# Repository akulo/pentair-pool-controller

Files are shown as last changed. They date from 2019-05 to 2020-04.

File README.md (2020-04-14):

# Pentair Pool Controller

For last couple of years, I have been looking for good automation system that I can use to automate my backyard pool and spa. All current systems available are outdated and overpriced. It is mind blowing to see how much Pentair, Zodiak or Hayward are charging for their systems. So, I decided to build my own.

It is powered by RaspberyPi running NodeJS, Node-Red, Node Red Dashboard coupled with 16 relays module and IntelliComm® II Interface Adapter. I really could have implemented software solution instead of overpriced adapter but I decided to focus on building hardware first. 

### Here is the view of AQUALINK® POWER CENTERS and Pool Controller Altelix enclosure:
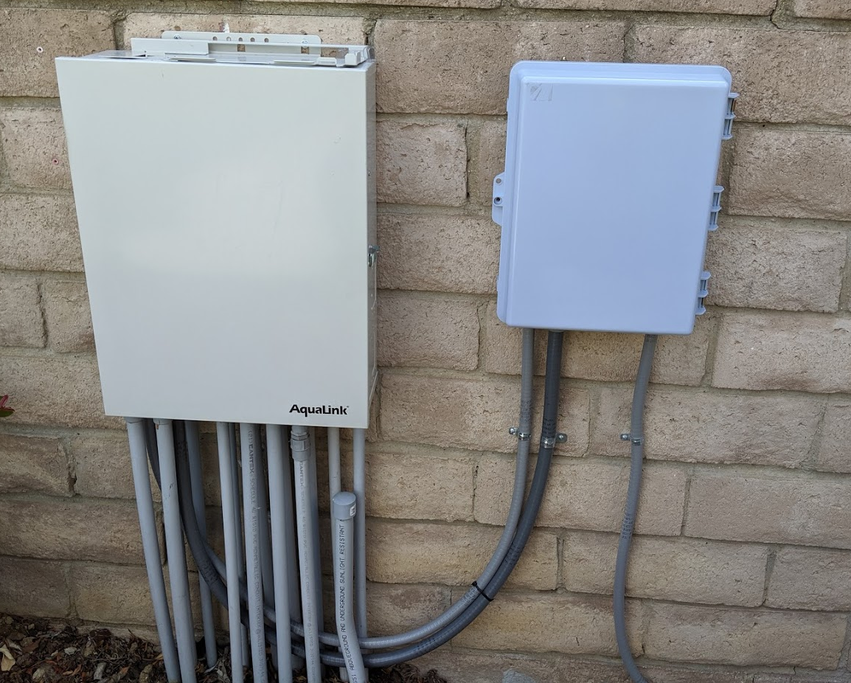
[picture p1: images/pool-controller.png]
Pentair Pool Controller


### View of assembled controller
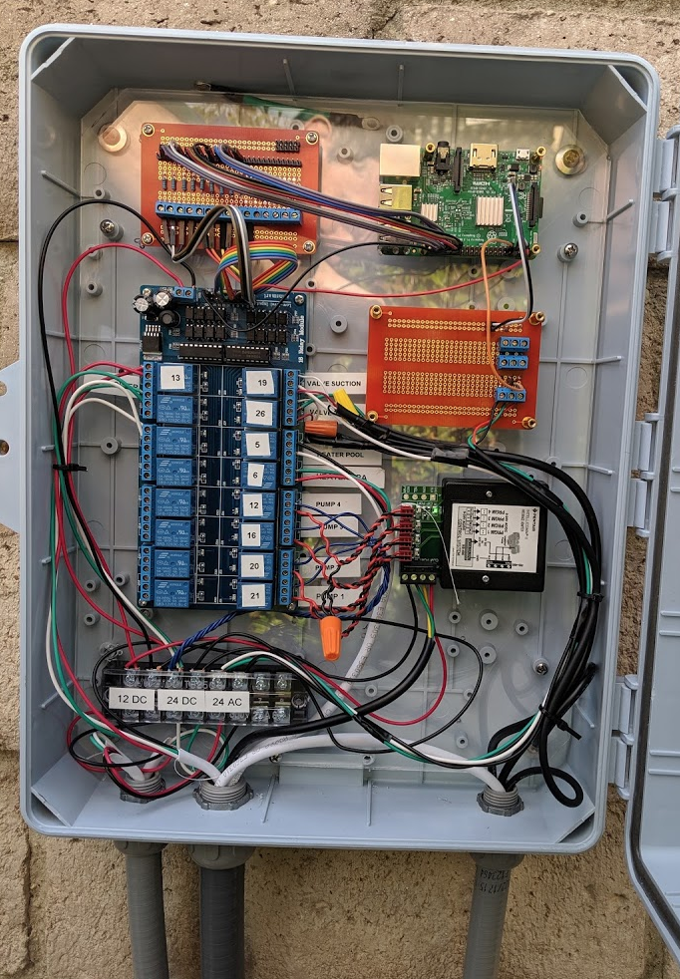
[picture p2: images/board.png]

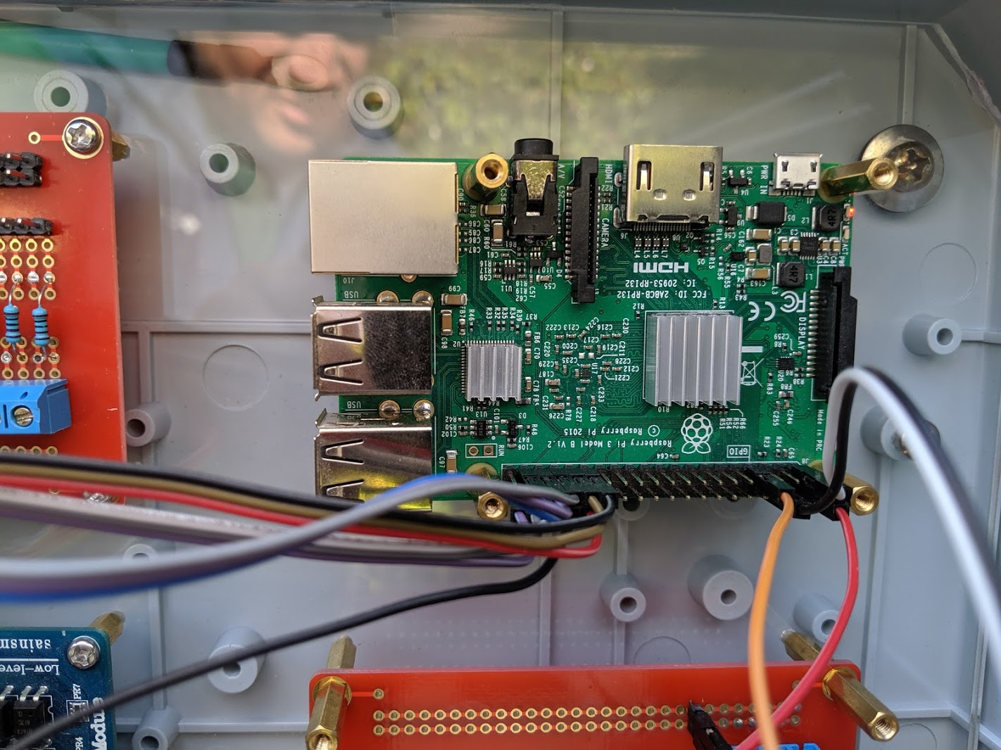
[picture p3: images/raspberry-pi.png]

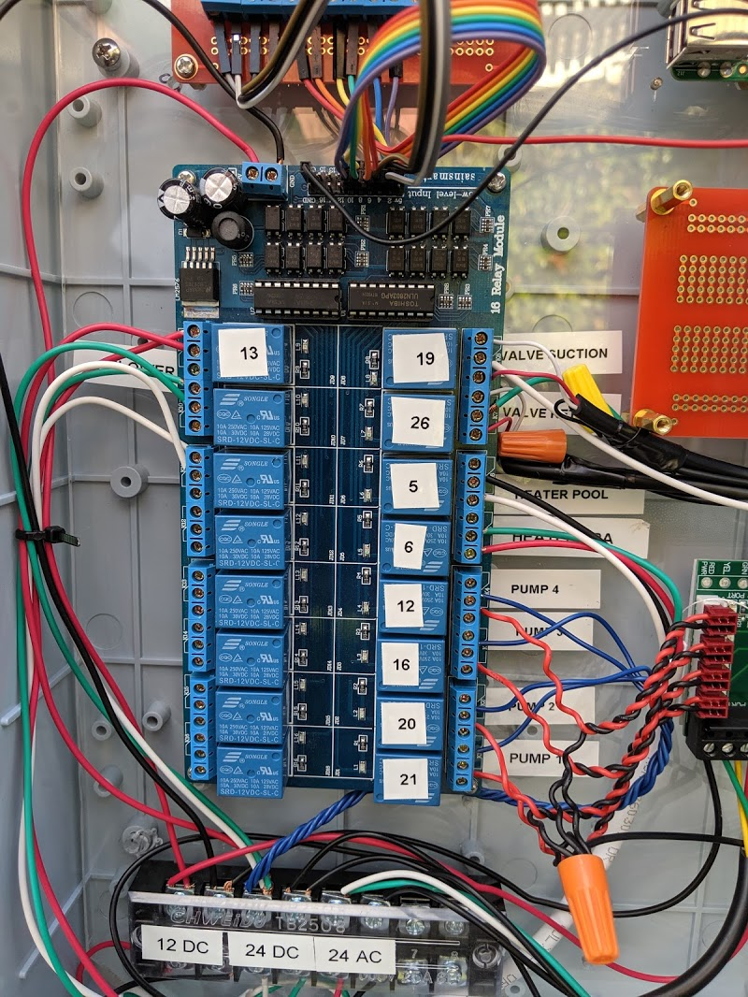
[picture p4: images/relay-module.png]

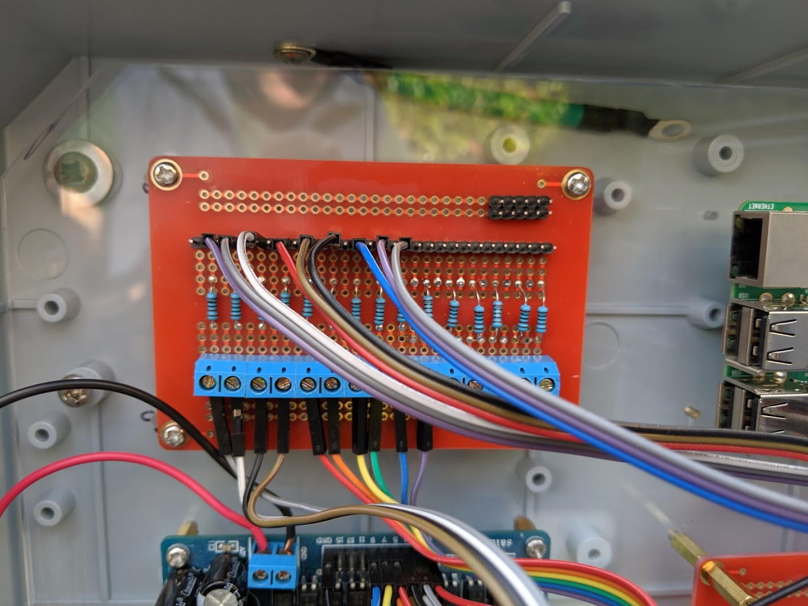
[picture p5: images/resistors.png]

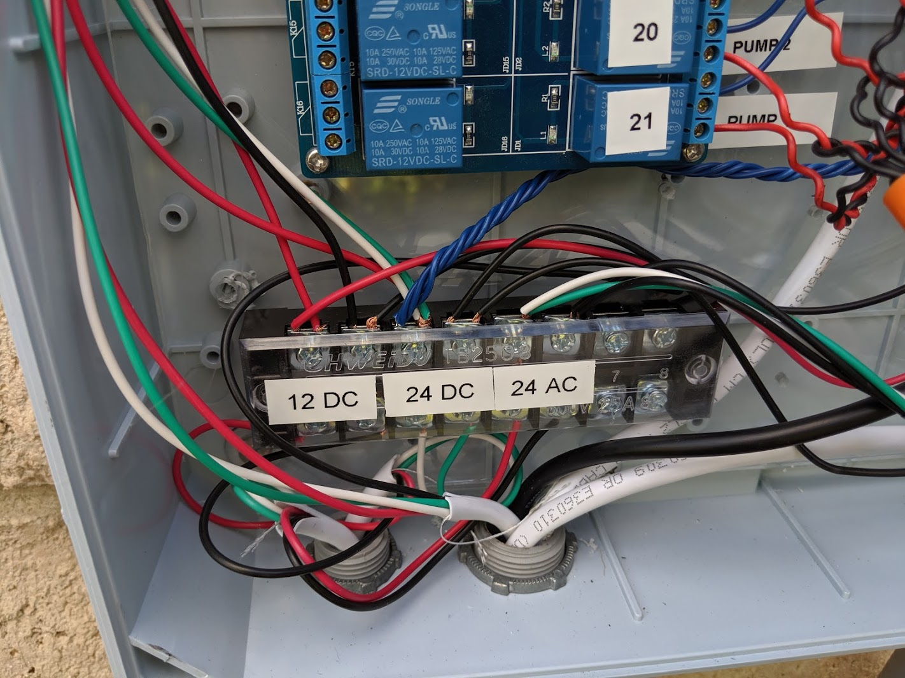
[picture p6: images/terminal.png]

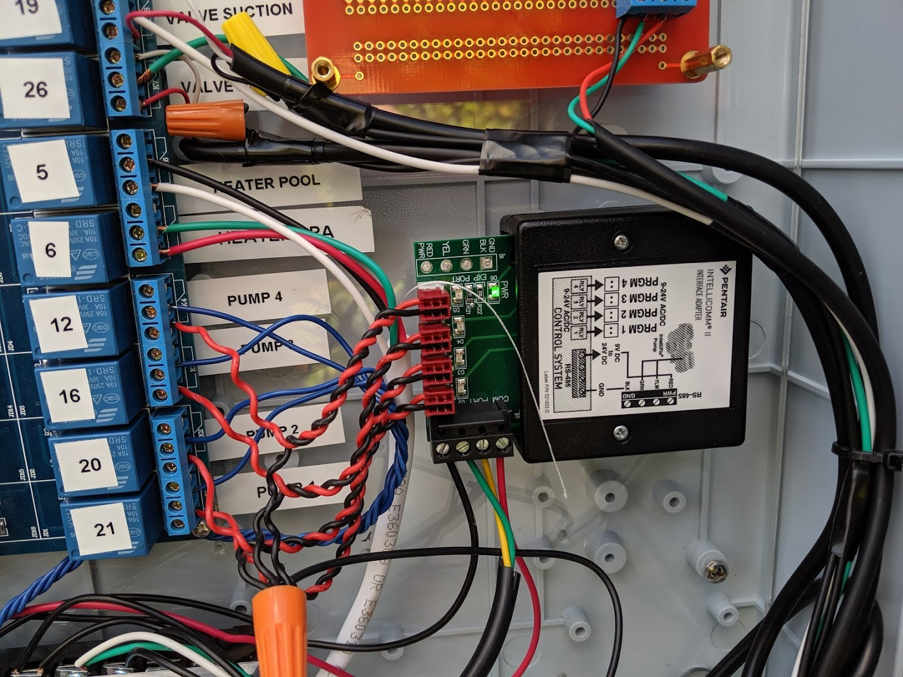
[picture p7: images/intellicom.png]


### View of Intermatic PE24VA Valve Actuators
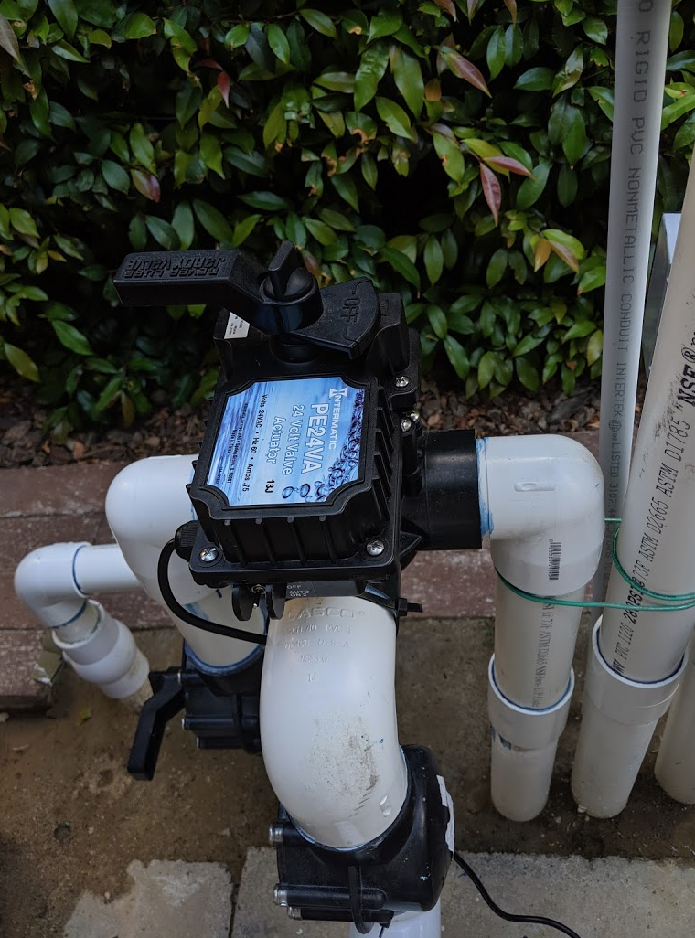
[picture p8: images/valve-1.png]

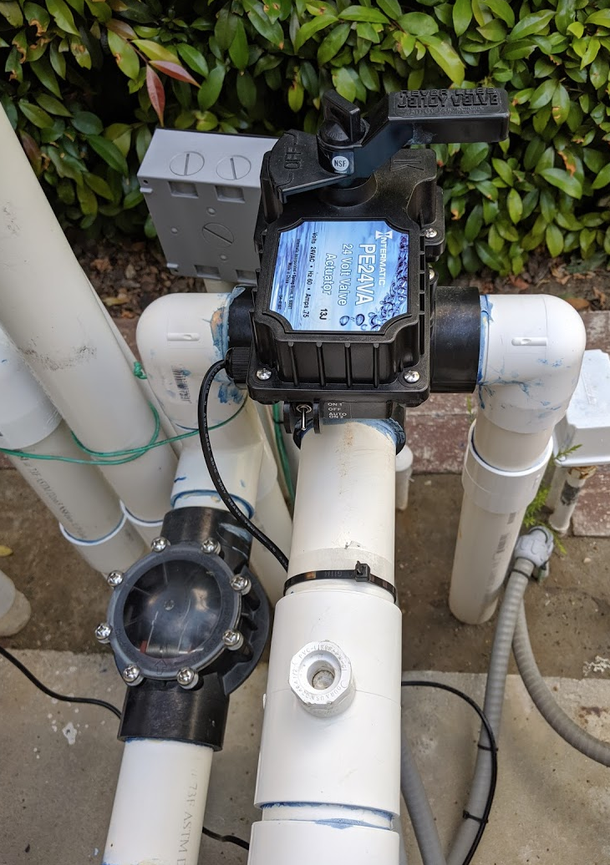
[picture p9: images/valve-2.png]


### View of sub-panel with breakers
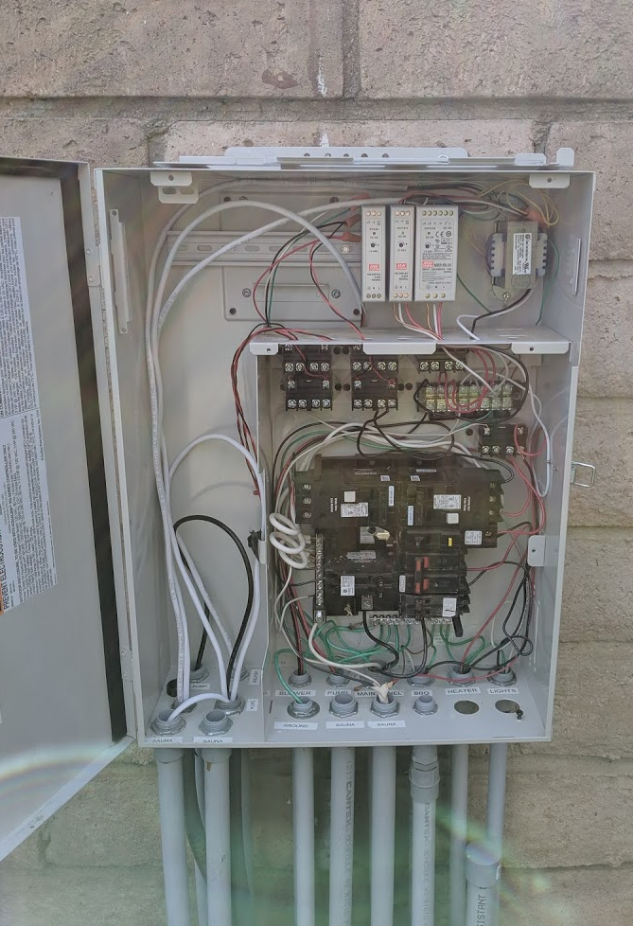
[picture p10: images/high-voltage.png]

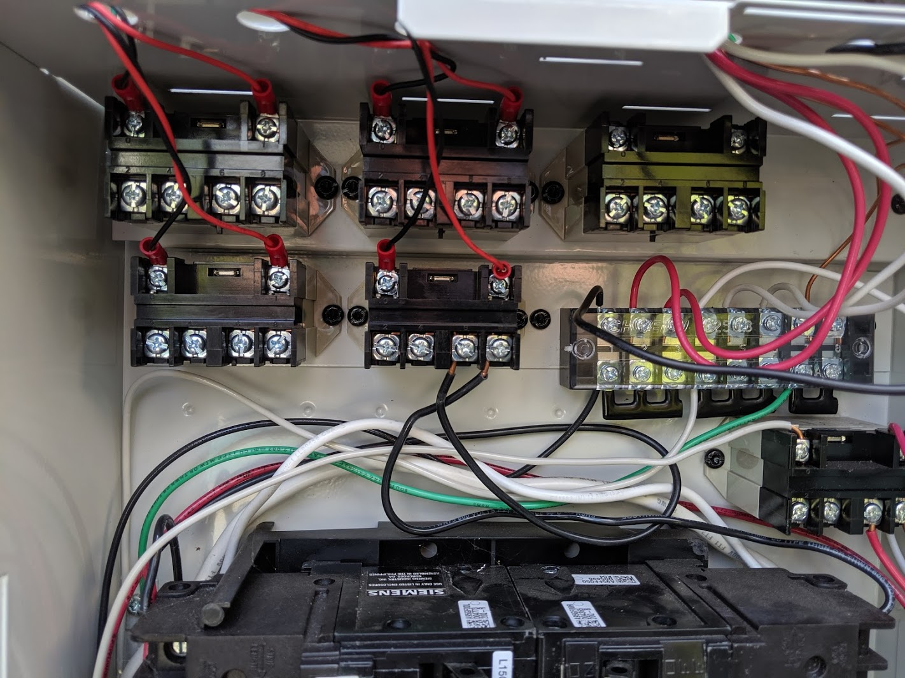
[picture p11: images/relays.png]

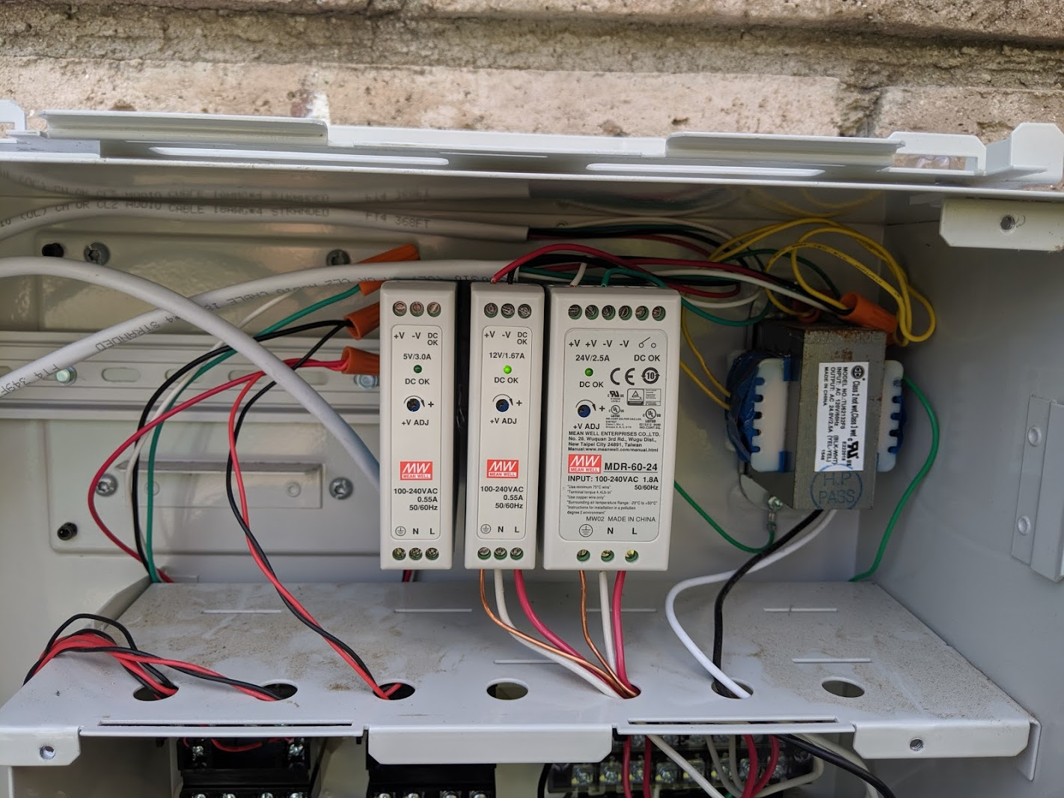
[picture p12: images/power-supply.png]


### Tempreture Sensors Assembly
I used DS18b20 Waterproof Temperature Sensors that I glued with [J-B Weld](https://www.homedepot.com/p/J-B-Weld-25-ml-ClearWeld-Quick-Set-Epoxy-Syringe-50112/204986141) epoxy to 1/2 in. MIP x 1/4 in. FIP Lead-Free Brass Pipe Hex Bushing and 1/4 in. x 1/4 in. MIP Lead-Free Brass Hose Barb Adapter. 

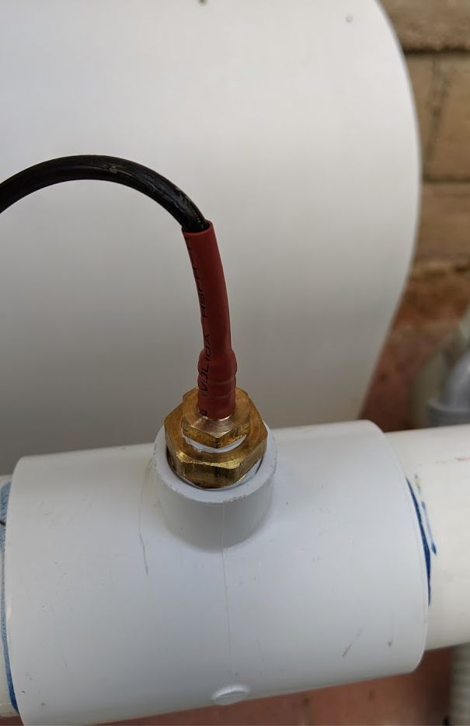
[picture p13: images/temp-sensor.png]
Pentair Pool Controller Tempreture Sensor

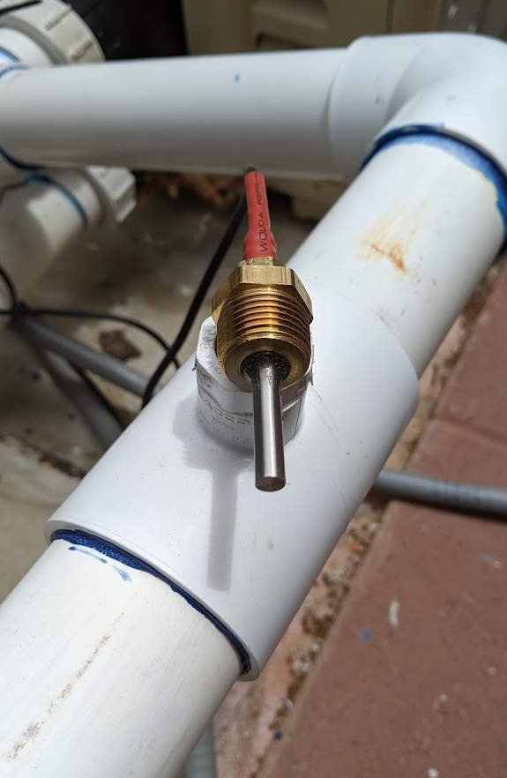
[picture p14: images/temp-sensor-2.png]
Pentair Pool Controller Tempreture Sensor


Parts:
1. [1/2 in. MIP x 1/4 in. FIP Lead-Free Brass Pipe Hex Bushing](https://www.homedepot.com/p/Everbilt-1-2-in-MIP-x-1-4-in-FIP-Lead-Free-Brass-Pipe-Hex-Bushing-802639/207176802)
1. [1/4 in. x 1/4 in. MIP Lead-Free Brass Hose Barb Adapter](https://www.homedepot.com/p/Everbilt-1-2-in-MIP-x-1-4-in-FIP-Lead-Free-Brass-Pipe-Hex-Bushing-802639/207176802)
1. [J-B Weld](https://www.homedepot.com/p/J-B-Weld-25-ml-ClearWeld-Quick-Set-Epoxy-Syringe-50112/204986141)

### FireTablet wall controller
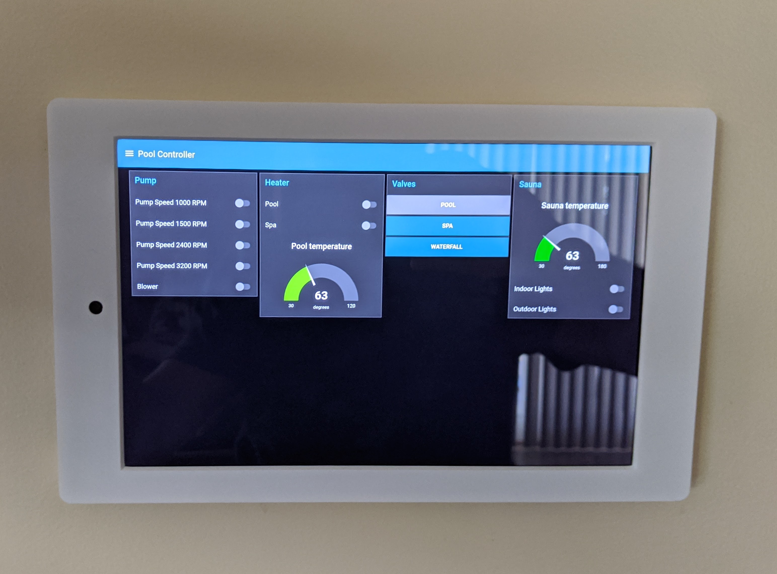
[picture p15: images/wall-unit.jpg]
Wall Unit


### Breadboard and Schematic
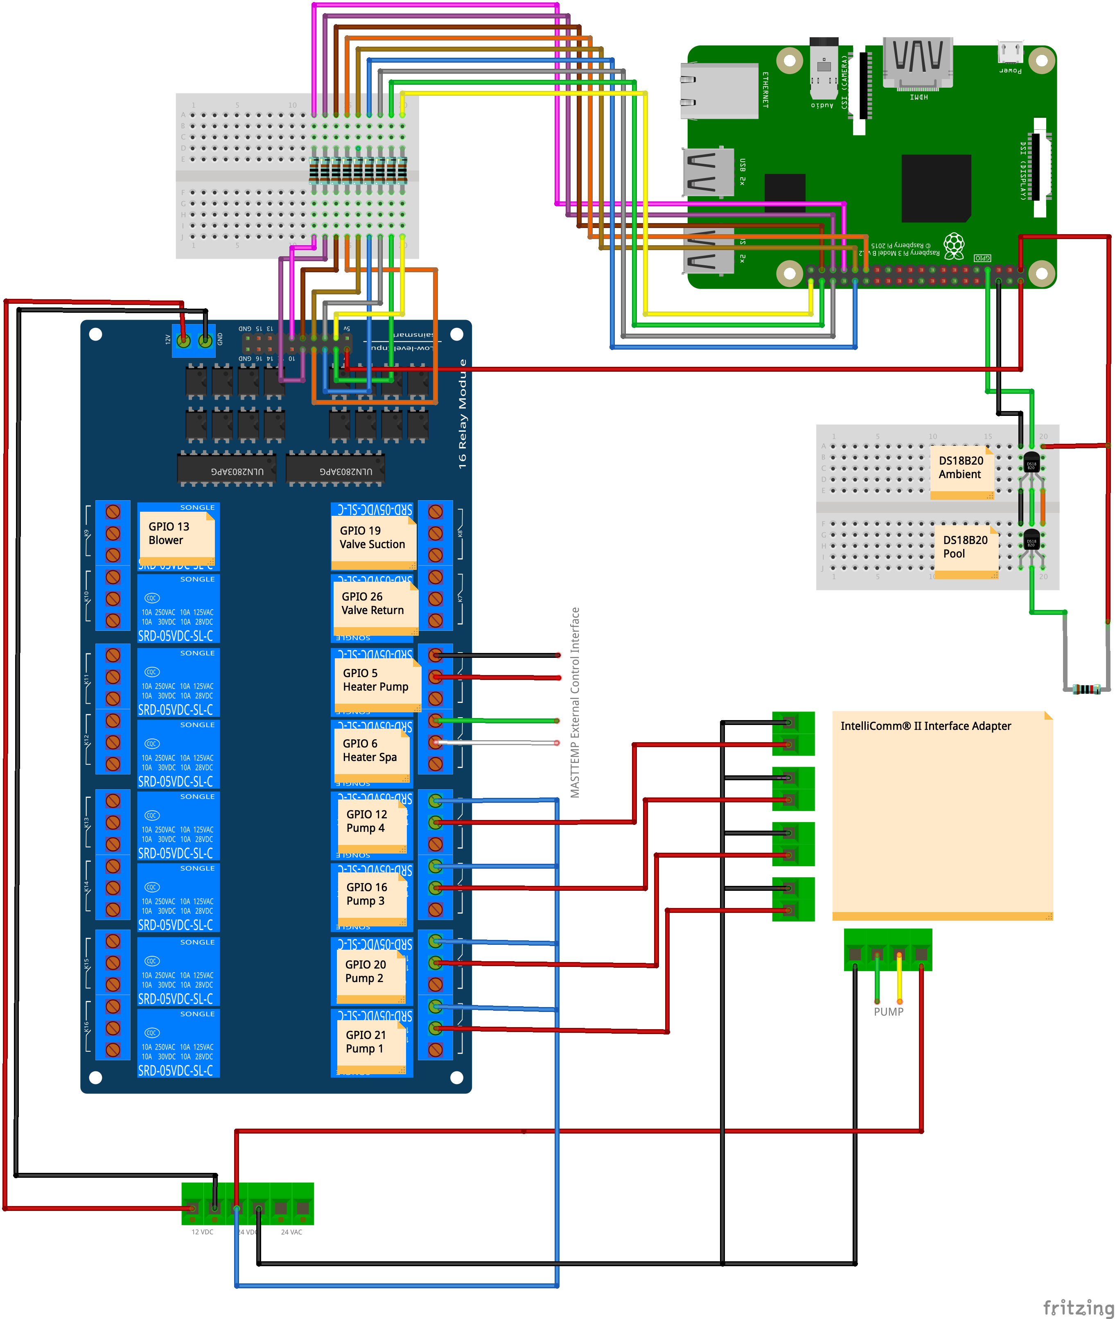
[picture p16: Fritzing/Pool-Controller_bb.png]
Pentair Pool Breadboard

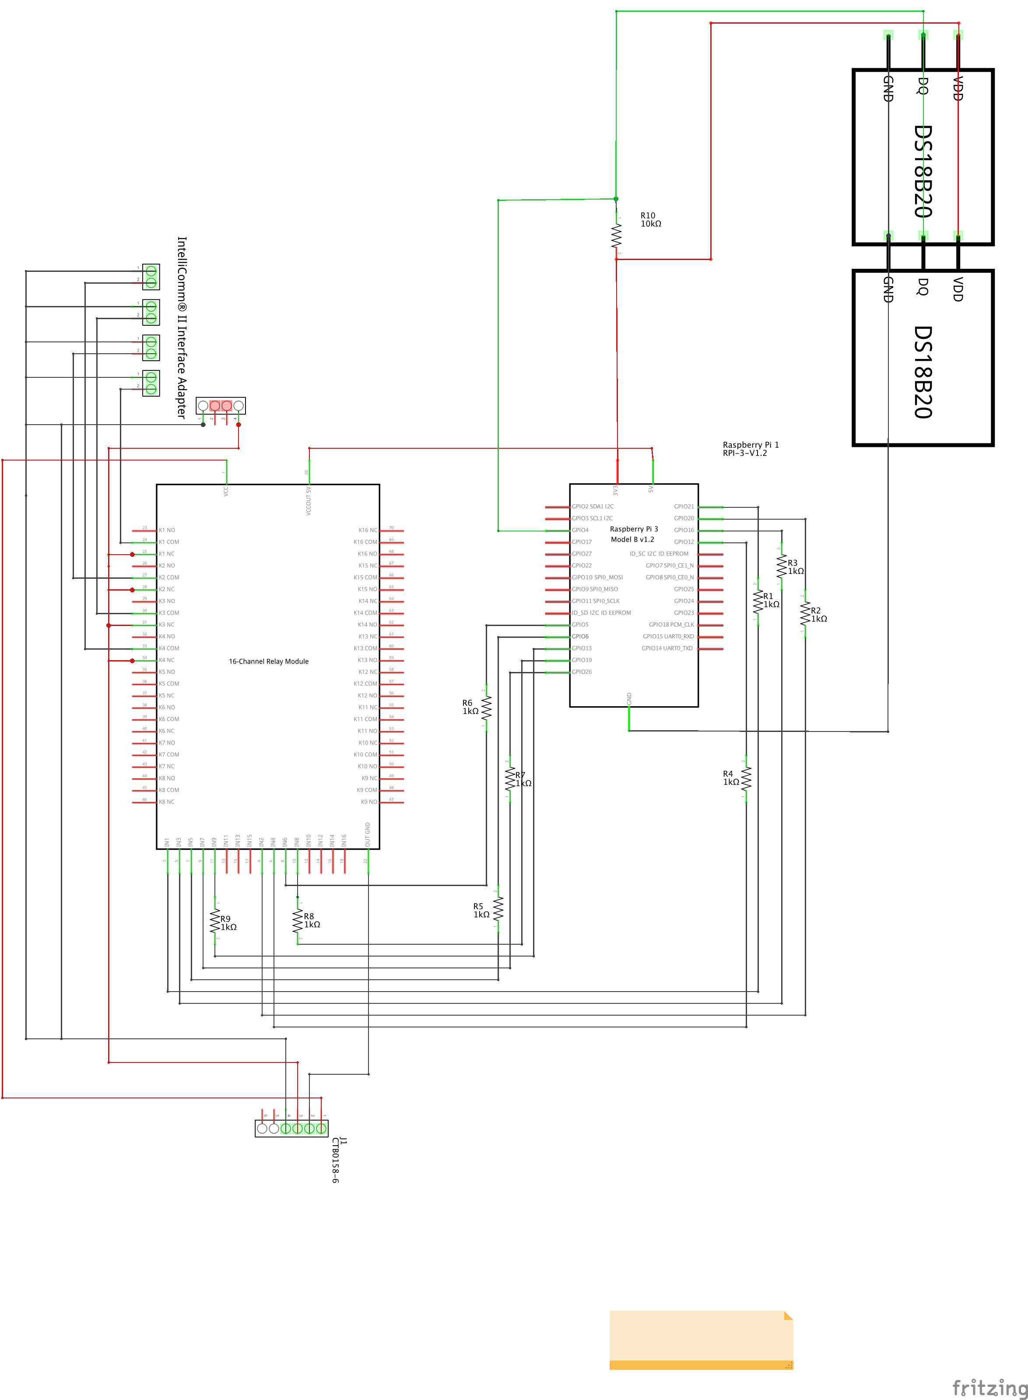
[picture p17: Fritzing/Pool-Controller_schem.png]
Pentair Pool Schematic


### Here is the list of the components I used:

1. [Raspberry Pi 3 Model B Board](https://www.amazon.com/Raspberry-Pi-MS-004-00000024-Model-Board/dp/B01LPLPBS8)
1. [SainSmart 16-Channel Relay Module](https://www.amazon.com/gp/product/B0057OC66U)
1. [IntelliComm® II Interface Adapter](https://www.pentair.com/en/products/pool-spa-equipment/pool-automation/intellicomm_ii_interfaceadapter.html)
1. [Altelix NEMA Enclosure 17x14x6](https://www.amazon.com/Raspberry-Pi-MS-004-00000024-Model-Board/dp/B01LPLPBS8)
1. [Omron G7L-2A-BUBJ-CB DC24 Relays](https://www.amazon.com/gp/product/B0057OC66U)
1. [8 Positions Dual Row 600V 25A Screw Terminals](https://www.amazon.com/gp/product/B0057OC66U)
1. [DS18b20 Waterproof Temperature Sensors](https://www.amazon.com/gp/product/B0057OC66U)
1. [Intermatic PE24VA Valve Actuators](https://www.amazon.com/Intermatic-PE24VA-Valve-Actuator-Black/dp/B002ZPJVV2)
1. [AQUALINK® POWER CENTERS Model 6614-LD](https://www.jandy.com/en/products/controls/system-components/power-centers/aqualink-power-center)
1. [IntelliFlo® VSF Variable Speed Pump](https://www.pentair.com/en/products/pool-spa-equipment/pool-pumps/intelliflo_vsf.html)
1. [MASTERTEMP HEATER](https://www.pentair.com/en/products/pool-spa-equipment/pool-heaters/mastertemp_heater/sku/460737.html)
1. [MEAN WELL MDR-60-24 DIN-Rail Power Supply 24V 2.5 Amp 60W](https://www.amazon.com/gp/product/B005T6OBFU)
1. [DIN Rail Power Supplies 20W 12V 1.67A](https://www.amazon.com/gp/product/B00MEKD6X2)
1. [MEAN WELL MDR-20-5 AC to DC DIN-Rail Power Supply 5V 3 Amp 15W](https://www.amazon.com/gp/product/B005T6RBSO)

### In future I am planning

1. Integrate my system with analog sensors like flow, pressure, pH, and current sensors.
1. Build wall unit controller using some old android tablet.
1. Integrate with Google Assistance and Alexa.
1. Install Time Series database with Graphana so I can start collecting and visualizing historical sensor data

### Useful References
1. [RS485 Adapter Software Implementation](https://github.com/tagyoureit/nodejs-poolController#rs485-adapter)
1. [SunTouch / QuickTouch RS-485 Protocol](https://docs.google.com/document/d/1M0KMfXfvbszKeqzu6MUF_7yM6KDHk8cZ5nrH1_OUcAc/edit?usp=drivesdk)

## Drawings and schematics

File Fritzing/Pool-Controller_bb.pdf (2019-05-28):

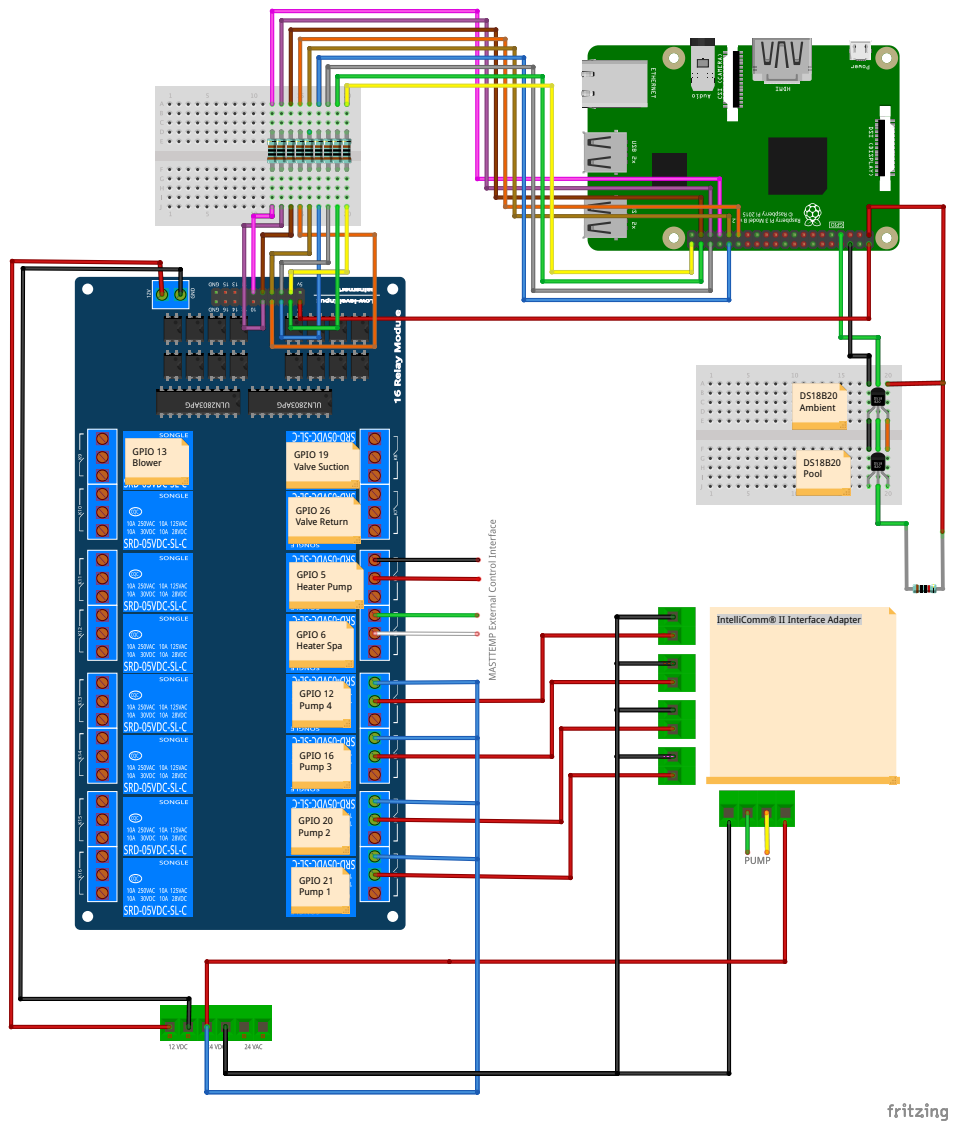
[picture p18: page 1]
bie; Blo; alv; tio

ol IntelliComm® II Interface

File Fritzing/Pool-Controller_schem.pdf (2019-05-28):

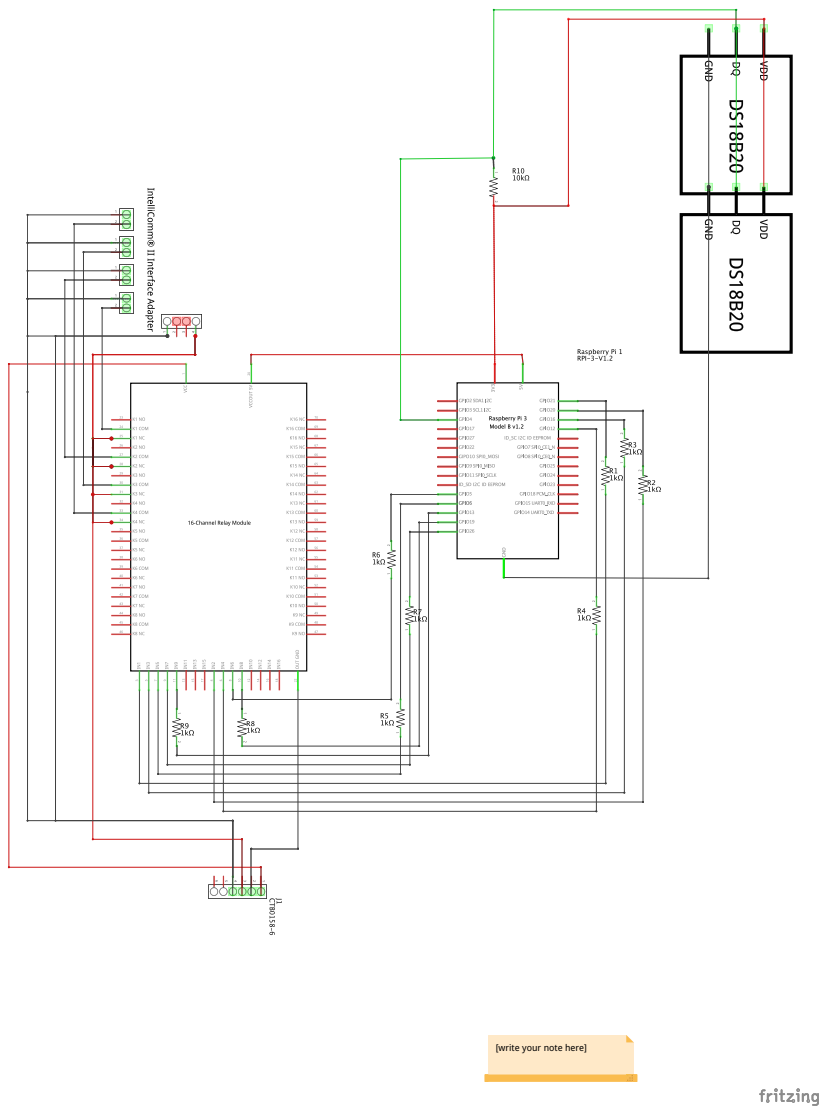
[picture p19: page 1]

[write your note here]

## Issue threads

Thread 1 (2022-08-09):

Pumps

spifftek70, 2022-08-09:
More of a question than an issue.  You have one Pentair IntelliCom II Interface Adapter for RS485 coms to the Intelliflo pump.  But then your Relay board lists multiple pumps...  The input is the yellow and green cable from one pump, but I'm not understanding how that leads to multiple pumps for control.   Also, can a Node-Red board be used in place of the IntelliCom II Interface Adapter?  Do you need one adapter per pump?

coreyfournier, 2023-01-10:
I think he is using the super flow vs that supports rs485 and 4 5v triggers for each speed. That's what I'm using.

akulo, 2023-01-10:
@spifftek70 Its not multiple pumps. Its just 4 different programs/speeds for same pump. I am using one Pentair IntelliCom II Interface Adapter and Intelliflo pump.

jaysalazar, 2023-06-17:
@akulo , Follow up question regarding the RS485 communication. How exactly are you setting the RPM settings for each program/speed?

spifftek70, 2023-06-17:
When setting up the schedule for your pool, it allows you to set the pump speed. You can also dynamically change the speed of the pump in the regular dashboard interface.

jaysalazar, 2023-06-18:
I think I am missing something, looking at the node red flow, I don't understand how you are able to send a command to change the speed of the pump. Is that what you meant by "regular dashboard interface"?

akulo, 2023-06-18:
yes on pump itself I preprogrammed 4 different speeds. All I do from node-red flow just trigger one of those speeds. I cant dynamically change speeds from my controller. All I can do is select one of the 4 pre-programmed speeds. Read your pump manual only certain programs allow such control as far as I remember.

jaysalazar, 2023-06-18:
Thanks for confirming, planning on using relays to trigger each speed. I found an example online, my wiring a slightly different but the concept is the same.

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

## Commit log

2019-05-28 power supply
2019-05-28 Temperature Sensors
2019-05-28 Add View of Intermatic PE24VA Valve Actuators
